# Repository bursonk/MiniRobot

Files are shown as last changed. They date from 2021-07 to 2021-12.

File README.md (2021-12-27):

# MiniRobot Design
Image of Robot
A mini robot built within sumo robot specifications designed to push blocks outside of the ring.  Built to run autonomous or remotely controlled with Bluetooth, as well as a programmable OLED display for debugging.

## Table of contents
* [General info](#general-info)
* [Technologies](#technologies)
* [Project Status](#project-status)
* [Features](#features)
* [acknowledgements](#acknowledgements)

## General info
This project contains the custom chassis and PCB design files I created for a University Design Project in February 2020. 

## Technologies
* Teensy3.6
* KiCad
* SolidWorks

## Project Status
Due to various manufactures of component boards, location of mounting holes may need to be altered.

### To Do List
- [x] Update files to reflect final design
- [ ] Complete Project Documentation

## Features
The sumo robot features a 10cm X 10cm Chassis.

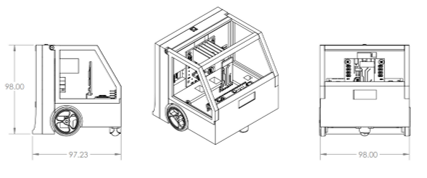
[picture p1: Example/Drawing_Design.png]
Robot Drawing


### Chassis

#### 3D printing

#### Threaded Inserts

### PCB

#### Soldering

#### Wiring and Connections

### Components

### Results

## Acknowledgements
A folder of SolidWorks parts with the electrical components used in the robot is included in this repository. 
Parts in this folder are used for the robot assembly design and were obtained from SolidWorks resources, from the manufacturer, or developed by me.

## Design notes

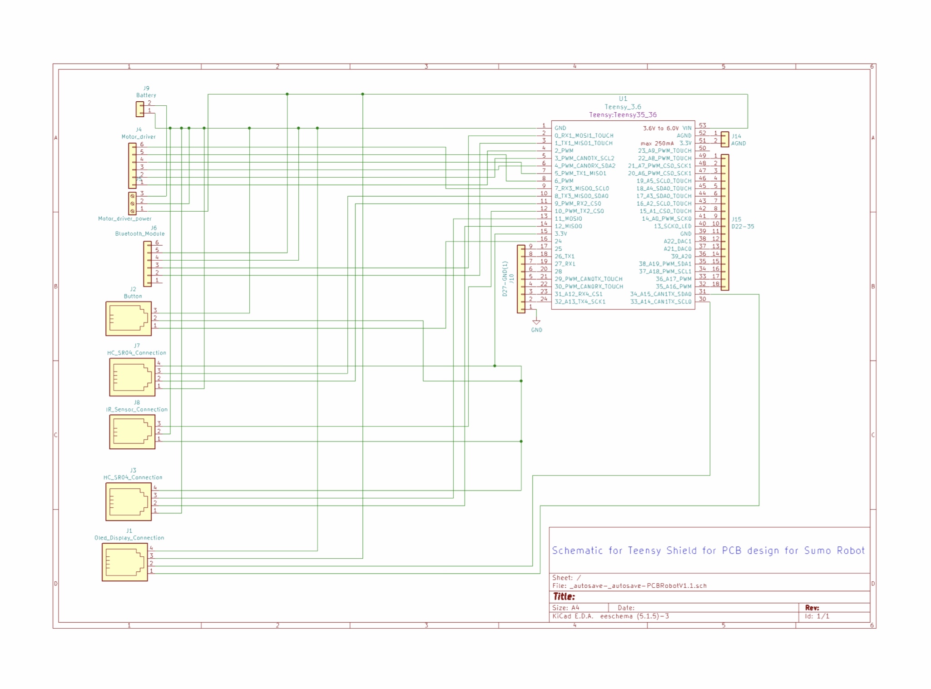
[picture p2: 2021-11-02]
Example/TeensyShieldSchematic.jpg

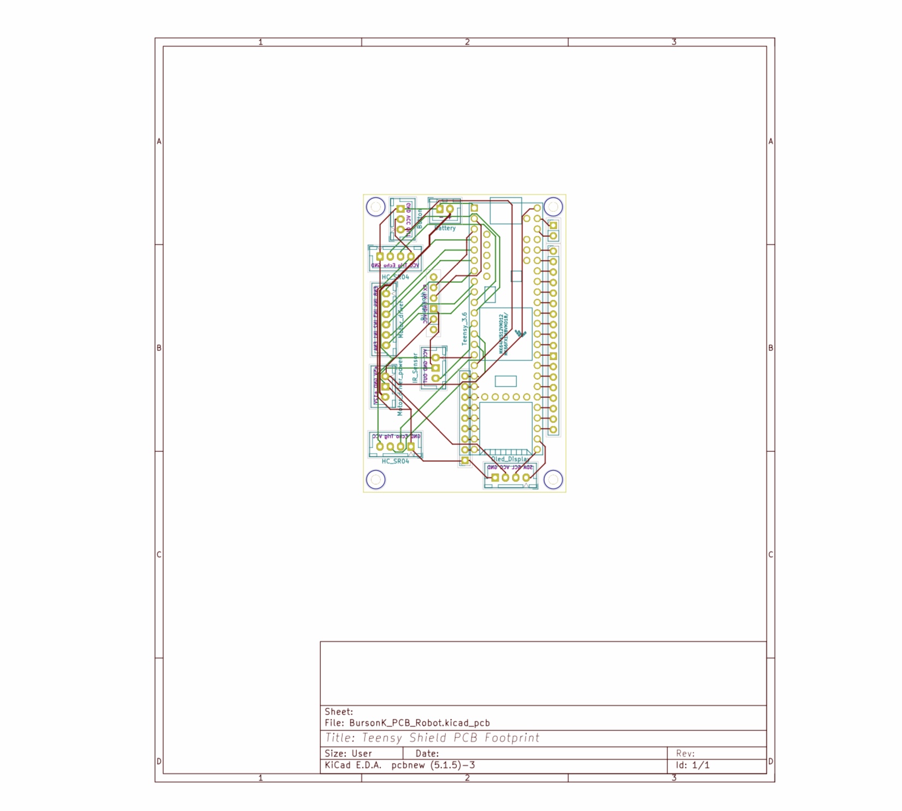
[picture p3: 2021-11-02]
Example/TeensyShieldLayout.jpg

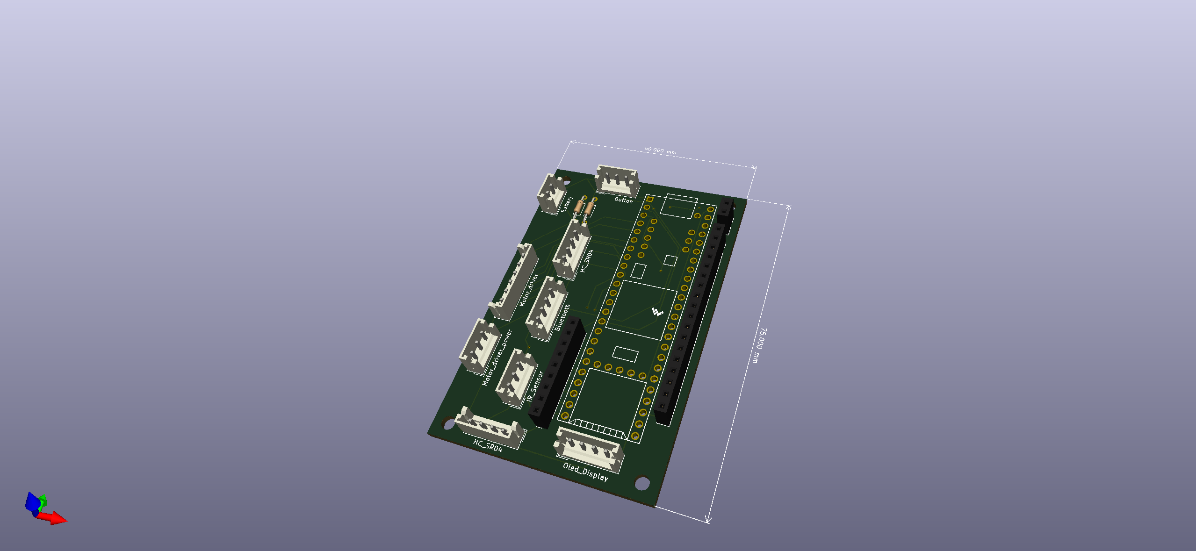
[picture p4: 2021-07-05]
Example/TeensyPCB_1.png

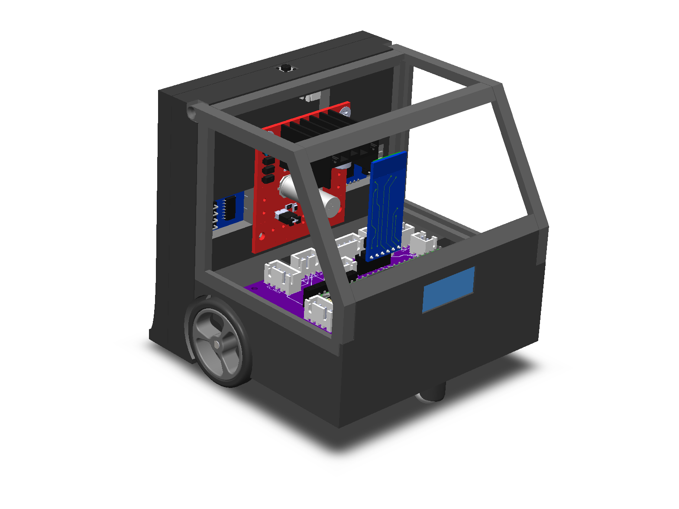
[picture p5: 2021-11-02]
Example/CAD_Robot_1.PNG

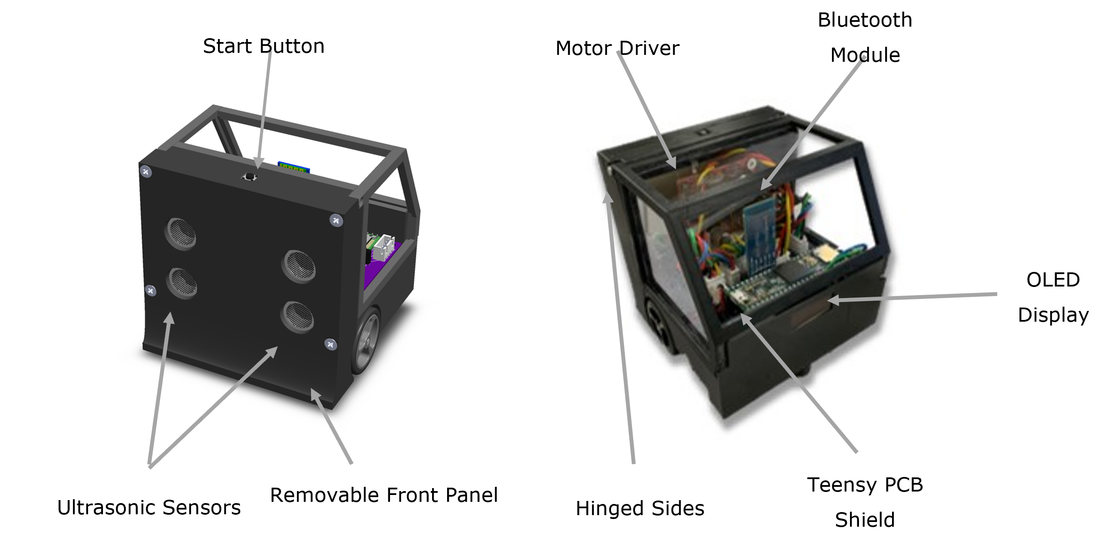
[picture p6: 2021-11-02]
Example/Layout_1.png

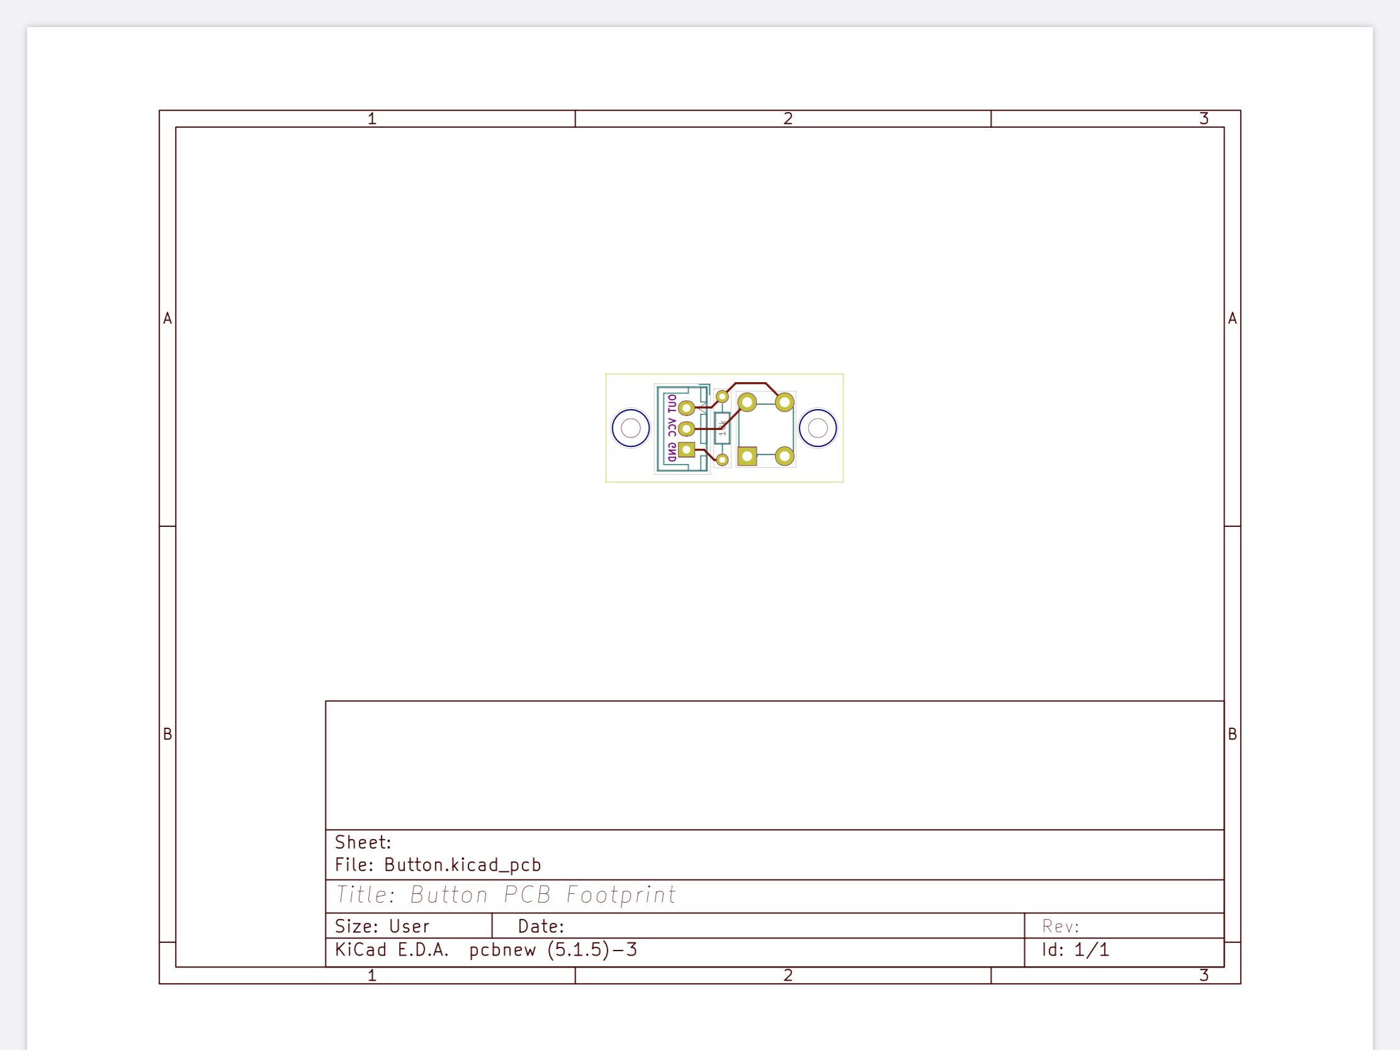
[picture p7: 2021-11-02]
Example/StartButtonLayout.PNG

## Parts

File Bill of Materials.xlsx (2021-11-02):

 | Bill of Materials
Main Category | Sub Category | Purchase Link | Notes | Part Number | Qty | Price | Total Price for Parts | Data Sheet
Microcontroller | Teensy 3.6 | PJRC (https://www.pjrc.com/store/teensy36.html) |  | TEENSY36 | 1 | $29.25 | $29.25 | Here (https://cdn.sparkfun.com/datasheets/Dev/Arduino/Boards/K66P144M180SF5RMV2.pdf)
Electronics | HC-SR04+ Ultrasonic Sensor | Amazon (https://www.amazon.com/gp/product/B07W1GD5F8/ref=ppx_yo_dt_b_asin_title_o05_s00?ie=UTF8&psc=1) | 2pcs included and need 2 | a19052200ux0126 | 1 | $7.73 | $7.73 | Here (https://cdn.sparkfun.com/datasheets/Sensors/Proximity/HCSR04.pdf)
 | IR Infrared Sensor | Amazon (https://www.amazon.com/HiLetgo-Infrared-Avoidance-Reflective-Photoelectric/dp/B07W97H2WS?s=industrial) | 10 pcs included, need 1 | B07W97H2WS | 1 | $7.99 | $7.99 | Here (https://components101.com/sites/default/files/component_datasheet/Datasheet%20of%20IR%20%20Sensor.pdf)
 | HC-05 Bluetooth Module | JSumo (https://www.jsumo.com/hc-05-bluetooth-module-serial-transceiver-module) |  | HC06BT | 1 | $6.85 | $6.85 | Here (http://www.electronicaestudio.com/docs/istd016A.pdf)
 | OLed Display Module | Amazon (https://www.amazon.com/gp/product/B079BN2J8V/ref=ppx_yo_dt_b_asin_title_o01_s00?ie=UTF8&psc=1) | 2pcs included, need 1 | 8541549353 | 1 | $10.99 | $10.99 | Here (https://cdn-shop.adafruit.com/datasheets/SSD1306.pdf)
 | L298N Motor Drive Controller | #VALUE! (https://www.amazon.com/Qunqi-Controller-Module-Stepper-Arduino/dp/B014KMHSW6?hvadid=167139094796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) |  | CECOMINOD012186 | 1 | $6.89 | $6.89 | Here (http://www.handsontec.com/dataspecs/L298N%20Motor%20Driver.pdf)
 | Mini Gear Motor | Pololu (https://www.pololu.com/product/997) | 150:1 Gearmotor - 6V | 997 | 2 | $15.95 | $31.90 | Here (https://www.pololu.com/file/0J1487/pololu-micro-metal-gearmotors-rev-4-2.pdf)
 | Tactile SPST Switch | ResiStore (https://resi.store/inventory/item.php?plu=855) |  | 855 | 1 | $0.05 | $0.05 | Here (https://resi.store/datasheets/spst.pdf)
 | 10k Resistor | ResiStore (https://resi.store/inventory/item.php?plu=190) |  | 190 | 1 | $0.05 | $0.05 | Here (https://resi.store/datasheets/resistor.pdf)
 | 9V Battery Holder with Switch | LedSupply (https://www.ledsupply.com/accessories/9v-battery-holder-switch-leads) |  | BH-9V-SWITCH | 1 | $1.69 | $1.69 | Here (https://www.ledsupply.com/accessories/9v-battery-holder-switch-leads)
Assembly | Wheel 32X7mm - Pair | Pololu (https://www.pololu.com/product/1087) |  | 1087 | 1 | $2.95 | $2.95 | Here (https://www.pololu.com/product-info-merged/1087)
 | Caster Ball | Pololu (https://www.pololu.com/product/950) | Pololu Ball Caster with 3/8″ Plastic Ball | 950 | 1 | $1.99 | $1.99 | Here (https://www.pololu.com/file/0J1636/pololu-ball-caster-with-0-375in-ball.pdf)
 | B6B-XH-A(LF)(SN) | Digikey (https://www.digikey.com/product-detail/en/jst-sales-america-inc/B6B-XH-A-LF-SN/455-2271-ND/1000381) | JST XH Connector 6x1 - Male | 455-2271-ND | 2 | $0.27 | $0.54 | Here (http://www.jst-mfg.com/product/pdf/eng/eXH.pdf)
 | B5B-XH-A(LF)(SN) | Digikey (https://www.digikey.com/product-detail/en/jst-sales-america-inc/B5B-XH-A-LF-SN/455-2270-ND/1530483) | JST XH Connector 5x1 - Male | 455-2270-ND | 1 | $0.25 | $0.25 | Here
 | B4B-XH-A(LF)(SN) | Digikey (https://www.digikey.com/product-detail/en/jst-sales-america-inc/B4B-XH-A-LF-SN/455-2249-ND/1651047) | JST XH Connector 4x1 - Male | 455-2249-ND | 6 | $0.21 | $1.26 | Here
 | B3B-XH-A(LF)(SN) | Digikey (https://www.digikey.com/product-detail/en/jst-sales-america-inc/B3B-XH-A-LF-SN/455-2248-ND/1651046) | JST XH Connector 3x1 - Male | 455-2248-ND | 5 | $0.19 | $0.95 | Here
 | B2B-XH-A(LF)(SN) | Digikey (https://www.digikey.com/product-detail/en/jst-sales-america-inc/B2B-XH-A-LF-SN/455-2247-ND/1651045) | JST XH Connector 2x1 - Male | 455-2247-ND | 1 | $0.15 | $0.15 | Here
 | XHP - 6 | Digikey (https://www.digikey.com/product-detail/en/jst-sales-america-inc/XHP-6/455-2218-ND/1651016) | JST XH Female Connector Housing 6x1 | 455-2218-ND | 2 | $0.14 | $0.28 | Here
 | XHP - 5 | Digikey (https://www.digikey.com/product-detail/en/jst-sales-america-inc/XHP-5/455-2268-ND/1125486) | JST XH Female Connector Housing 5x1 | 455-2268-ND | 1 | $0.12 | $0.12 | Here
 | XHP - 4 | Digikey (https://www.digikey.com/product-detail/en/jst-sales-america-inc/XHP-4/455-2267-ND/683353) | JST XH Female Connector Housing 4x1 | 455-2267-ND | 6 | $0.10 | $0.60 | Here
 | XHP - 3 | Digikey (https://www.digikey.com/product-detail/en/jst-sales-america-inc/XHP-3/455-2219-ND/1651017) | JST XH Female Connector Housing 3x1 | 455-2219-ND | 5 | $0.10 | $0.50 | Here
 | XHP - 2 | Digikey (https://www.digikey.com/product-detail/en/jst-sales-america-inc/XHP-2/455-2266-ND/555485) | JST XH Female Connector Housing 2x1 | 455-2266-ND | 1 | $0.10 | $0.10 | Here
 | Brass Knurled Threaded Insert | Amazon (https://www.amazon.com/gp/product/B0784VYCYY/ref=ppx_yo_dt_b_asin_title_o04_s00?ie=UTF8&psc=1) | 250-Pcs M2 / M3 /M4 Assortment Kit | HBN-250 | 1 | $15.98 | $15.98 | Here (https://www.pemnet.com/bulletins_A4/sidata_A4.pdf)
 | M1.6 Thread Brass Knurled Insert | Amazon (https://www.amazon.com/gp/product/B07TTQXVQH/ref=ppx_yo_dt_b_asin_title_o06_s00?ie=UTF8&psc=1) | 50PCS M1.6 x 4mm | QXAD0072 | 1 | $4.59 | $4.59 | Here
 | M1.6 x 6mm Screws | Wilco | M1.6 screw 6mm length |  | 8 | $0.20 | $1.60
 | M2 x 4mm Screws | HomeDepot (https://www.homedepot.com/p/Everbilt-M2-0-4-x-4-mm-Phillips-Flat-Head-Stainless-Steel-Machine-Screw-2-Pack-843438/204852270) | 4mm Phillips flathead machine screw 2pcs | 794439 | 3 | $0.40 | $1.20
 | M2 x 8mm Screws | HomeDepot (https://www.homedepot.com/p/Everbilt-M2-0-4-x-8-mm-Phillips-Flat-Head-Stainless-Steel-Machine-Screw-2-Pack-843458/204852267) | 8mm Phillips flathead machine screw 2pcs | 795552 | 1 | $0.54 | $0.54
 | M2 x 10mm Screws | HomeDepot (https://www.homedepot.com/p/Everbilt-M2-0-4-x-10-mm-Phillips-Flat-Head-Stainless-Steel-Machine-Screw-2-Pack-843468/204852266) | 10mm Phillips flathead machine screw 2pcs | 790787 | 1 | $0.40 | $0.40
 | M3 x 6mm Screws | HomeDepot (https://www.homedepot.com/p/Everbilt-M3-0-5-x-6-mm-Phillips-Flat-Head-Zinc-Plated-Machine-Screw-3-Pack-841638/204849605) | 6mm Phillips flathead machine screw 3pcs | 903113 | 3 | $0.50 | $1.50
 | M3 x 8mm Screws | HomeDepot (https://www.homedepot.com/p/Everbilt-M3-0-5-x-8-mm-Phillips-Flat-Head-Stainless-Steel-Machine-Screw-2-Pack-843618/204849557) | 8mm Phillips flathead machine screw 2pcs | 513007 | 1 | $0.54 | $0.54
 | M3 x 10mm Screws | HomeDepot (https://www.homedepot.com/p/Everbilt-M3-0-5-x-10-mm-Phillips-Flat-Head-Stainless-Steel-Machine-Screw-2-Pack-843628/204849556) | 10mm Phillips flathead machine screw 2pcs | 796645 | 3 | $0.65 | $1.95
Custom Items | 3D Printed Frame
 | Teensy Shield - PCB Board
 | Button Module - PCB Board
 | Acrylic Cut Windows
 | Total Cost For Materials |  |  |  | $141.38

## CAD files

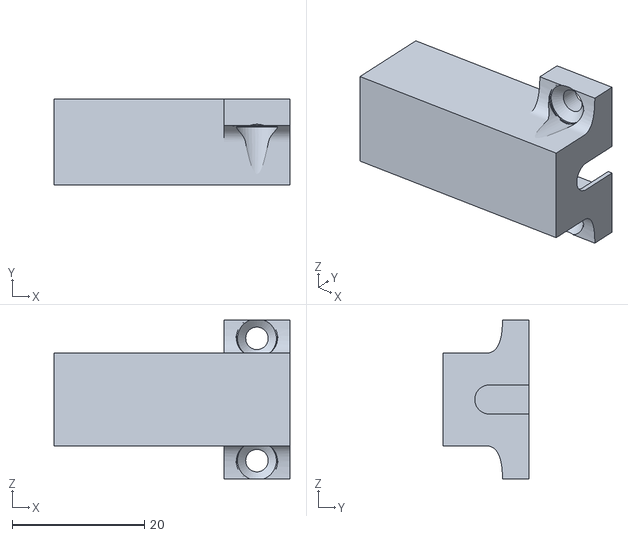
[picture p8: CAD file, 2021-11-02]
Custom Chassis Parts (.stl)/mount_v2.STL
35.7 x 13.0 x 24.0

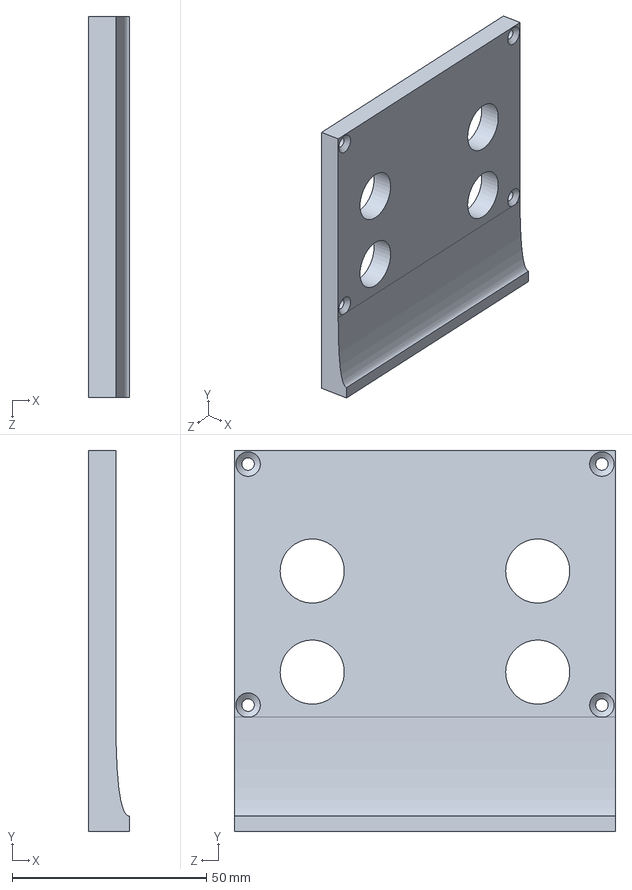
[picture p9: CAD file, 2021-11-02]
Robot SolidWorks Files/Front_Shield.SLDPRT
10.5 x 98.0 x 98.0 mm

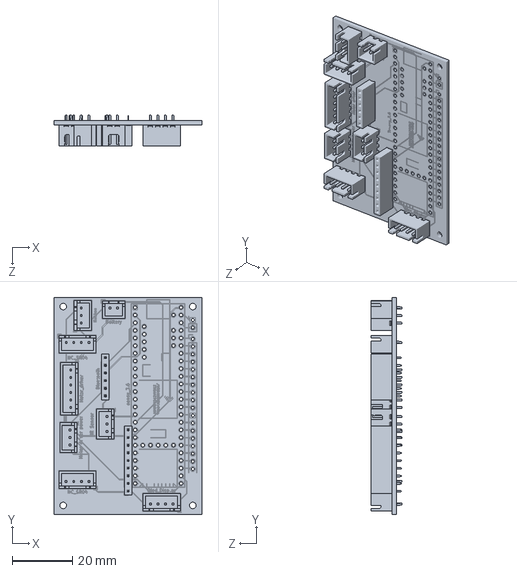
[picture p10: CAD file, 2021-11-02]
Robot SolidWorks Files/Purchased Components Parts/PCB_Bot.SLDPRT
49.0 x 72.0 x 10.4 mm

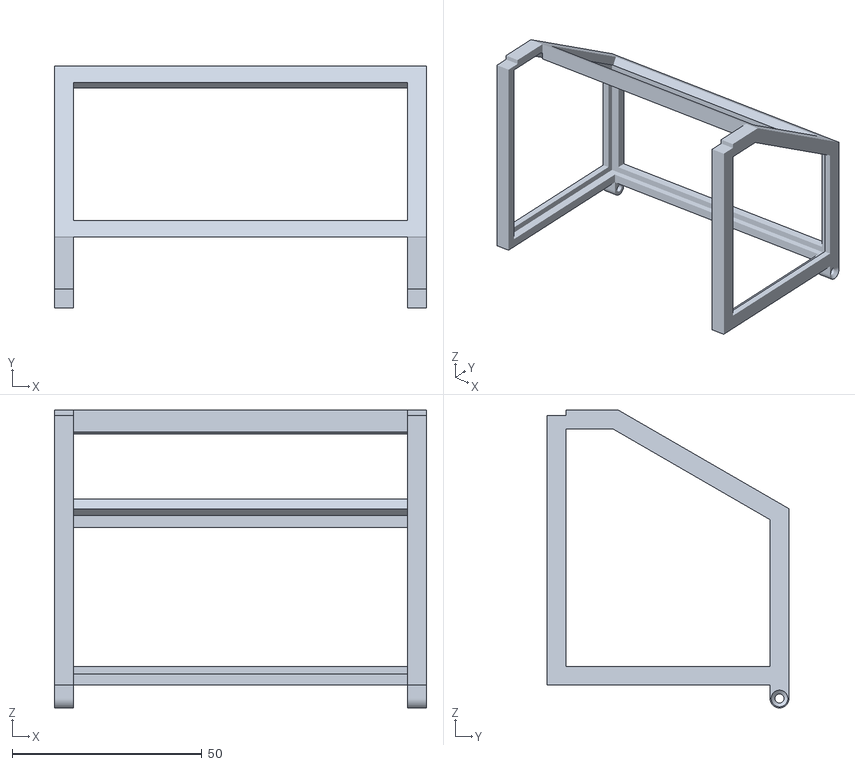
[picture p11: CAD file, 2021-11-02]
Custom Chassis Parts (.stl)/TopV2.STL
98.0 x 63.7 x 78.5

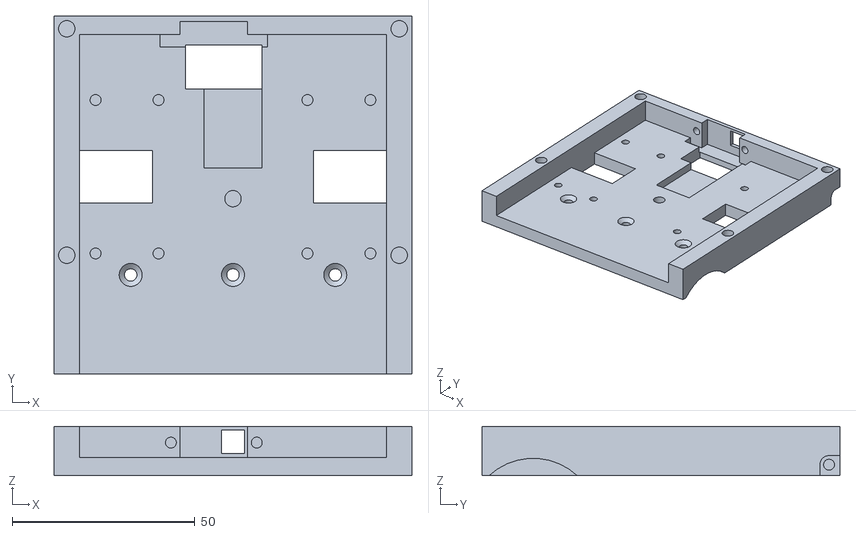
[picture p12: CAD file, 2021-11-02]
Custom Chassis Parts (.stl)/SensorMount_V2.STL
98.0 x 98.0 x 13.5

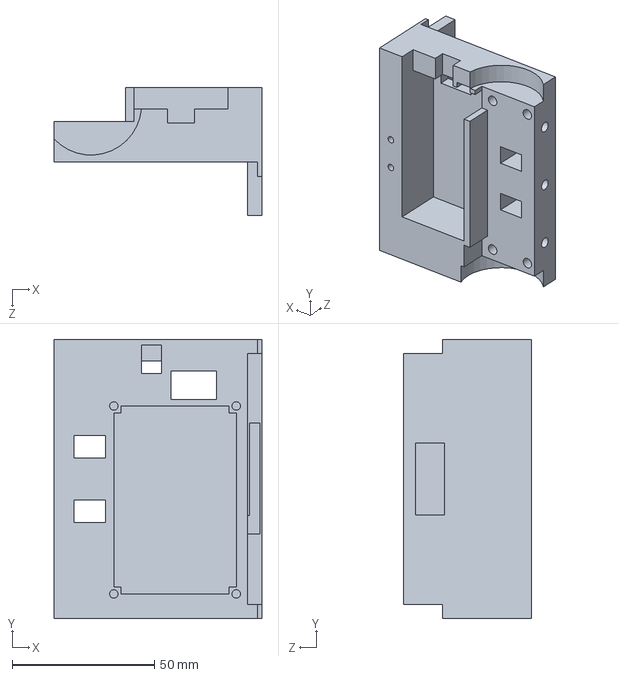
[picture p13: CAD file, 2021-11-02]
Robot SolidWorks Files/Base.SLDPRT
73.0 x 98.0 x 45.0 mm

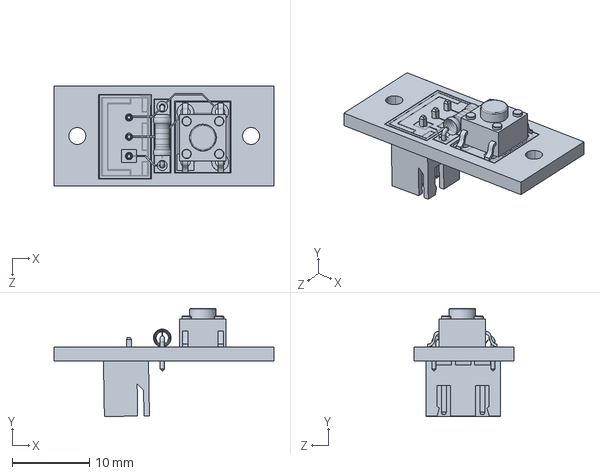
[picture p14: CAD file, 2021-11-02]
Robot SolidWorks Files/Purchased Components Parts/Button_PCB.SLDPRT
28.5 x 14.0 x 13.0 mm

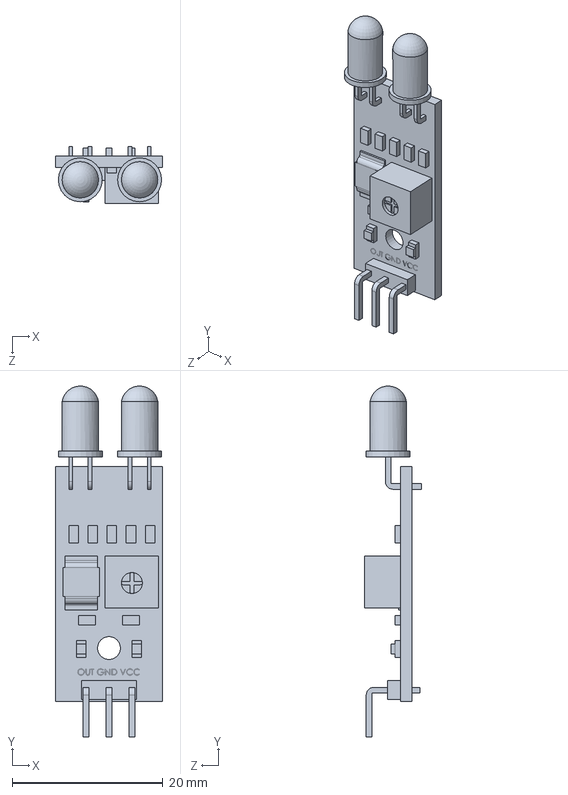
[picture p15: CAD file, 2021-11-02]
Robot SolidWorks Files/Purchased Components Parts/IR Sensor (FC51).SLDPRT
14.2 x 46.6 x 7.62 mm

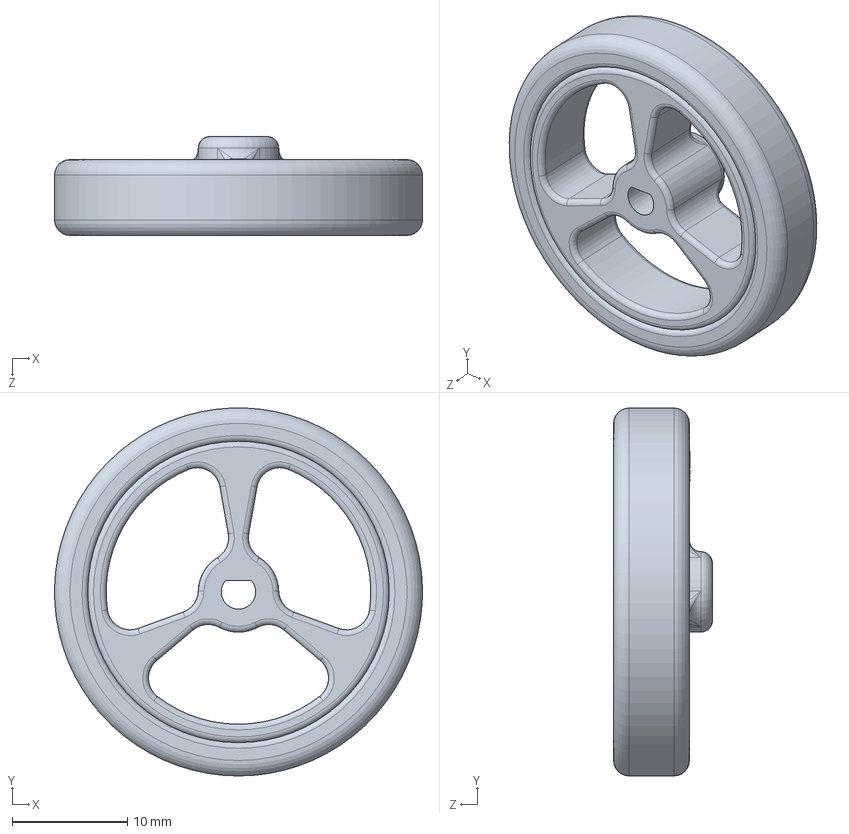
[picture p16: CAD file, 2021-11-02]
Robot SolidWorks Files/Purchased Components Parts/pololu-wheel-32x7mm-black.SLDPRT
32.0 x 32.0 x 8.60 mm

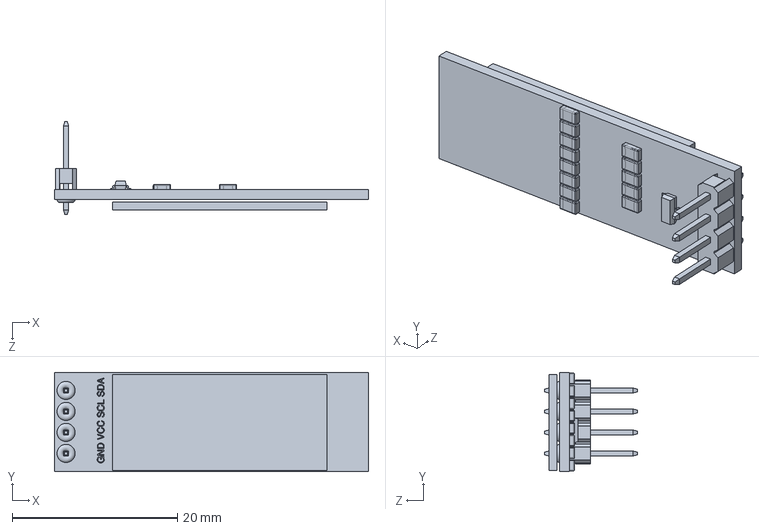
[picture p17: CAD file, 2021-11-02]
Robot SolidWorks Files/Purchased Components Parts/OLED 128x32 Display.SLDPRT
38.0 x 12.0 x 11.2 mm

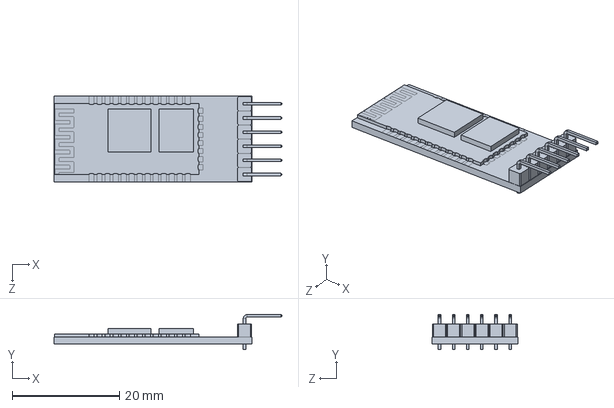
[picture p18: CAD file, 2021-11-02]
Robot SolidWorks Files/Purchased Components Parts/HC-05_Bluetooth.SLDPRT
42.6 x 6.55 x 16.0 mm

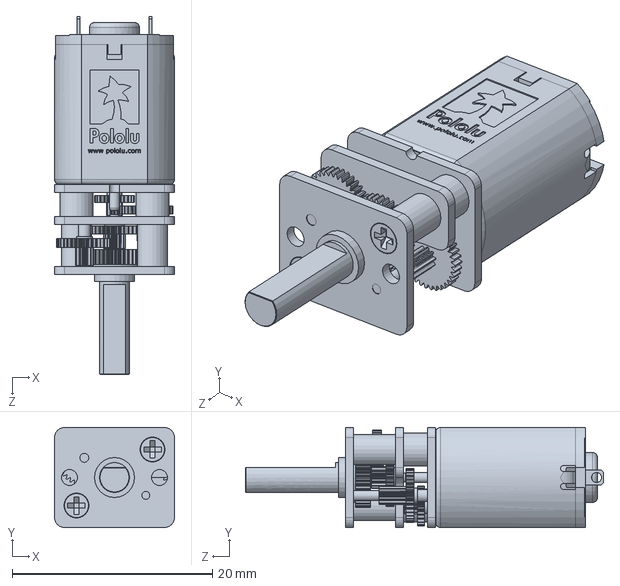
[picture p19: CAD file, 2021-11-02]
Robot SolidWorks Files/Purchased Components Parts/micro-metal-gearmotor-standard (1).SLDPRT
12.0 x 10.0 x 35.8 mm

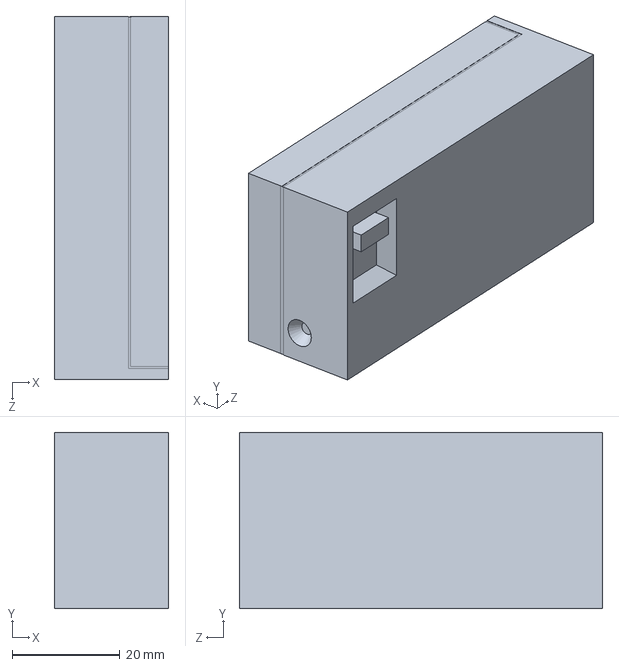
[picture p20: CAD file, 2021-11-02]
Robot SolidWorks Files/Purchased Components Parts/BatteryEnclosure.SLDPRT
21.2 x 32.8 x 67.5 mm

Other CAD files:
Robot SolidWorks Files/mount_v2.SLDPRT
Custom Chassis Parts (.stl)/Front_ShieldV2.STL
Robot SolidWorks Files/TopV2.SLDPRT
Custom Chassis Parts (.stl)/Base_V2.STL
Robot SolidWorks Files/SensorMount.SLDPRT
Custom Chassis Parts (.stl)/Archive/Base.STL
Custom Chassis Parts (.stl)/Archive/Front_Shield.STL
Custom Chassis Parts (.stl)/Archive/SensorMount.STL
Custom Chassis Parts (.stl)/Archive/SensorMountV2.1.STL
Custom Chassis Parts (.stl)/Archive/Side1.STL
Custom Chassis Parts (.stl)/Archive/Side2.STL
Custom Chassis Parts (.stl)/Archive/Sides.STL
Custom Chassis Parts (.stl)/Archive/Top1.STL
Custom Chassis Parts (.stl)/Archive/Top2.STL
Custom Chassis Parts (.stl)/Archive/Top3.STL
Custom Chassis Parts (.stl)/Archive/TopV2.1.STL
Custom Chassis Parts (.stl)/Archive/mount.STL
Robot SolidWorks Files/Archived Chassis SolidWorks Parts/Side1.SLDPRT
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

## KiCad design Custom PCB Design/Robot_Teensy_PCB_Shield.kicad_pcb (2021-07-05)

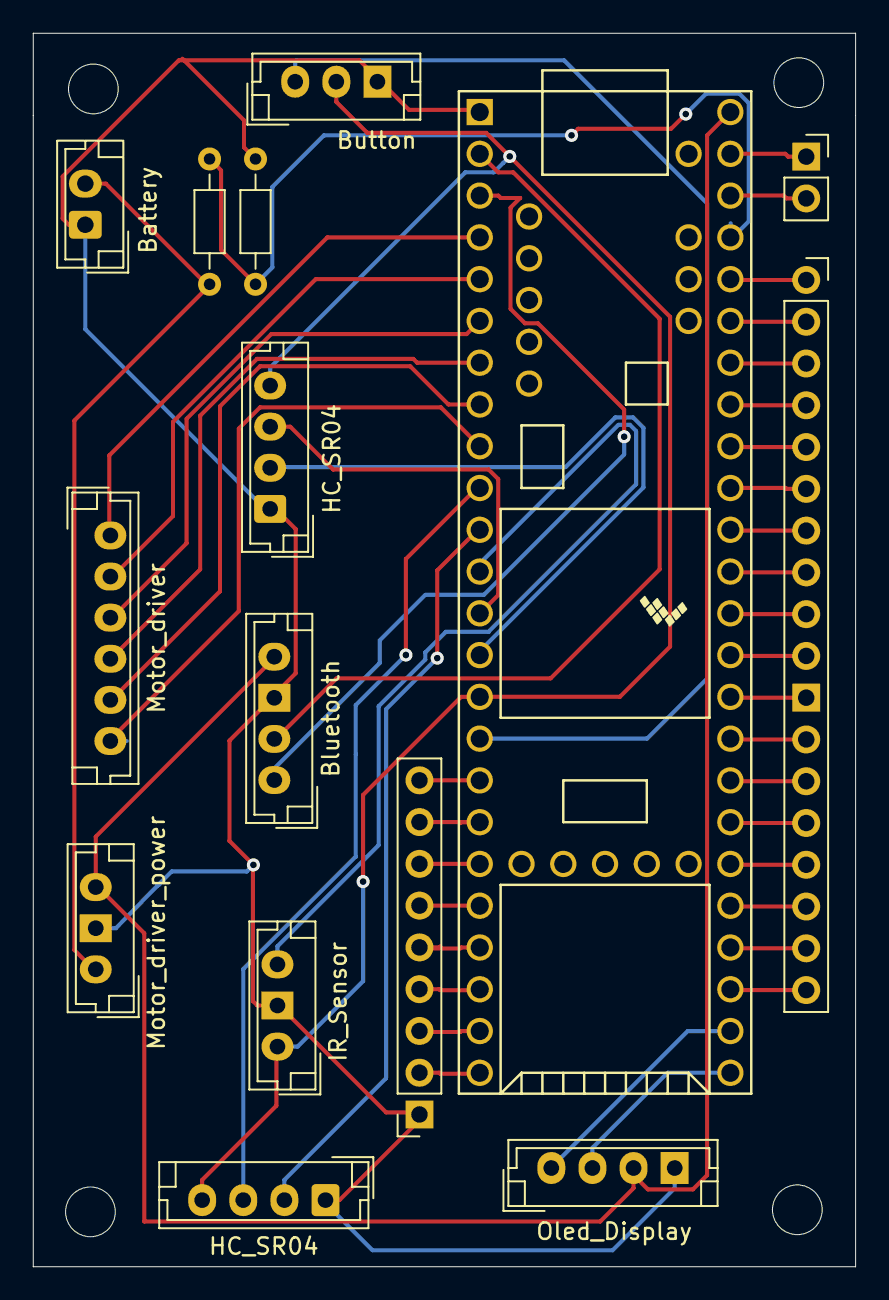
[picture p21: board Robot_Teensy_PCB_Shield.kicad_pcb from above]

Board: 2 copper layers, 50.0 x 75.0 mm, 9 parts (0 on the bottom side), 4 nets.

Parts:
Battery: JST_EH_B2B-EH-A_1x02_P2.50mm_Vertical
Bluetooth: JST_EH_B4B-EH-A_1x04_P2.50mm_Vertical
Button: JST_EH_B3B-EH-A_1x03_P2.50mm_Vertical
HC_SR04, HC_SR04#2: JST_EH_B4B-EH-A_1x04_P2.50mm_Vertical
IR_Sensor: JST_EH_B3B-EH-A_1x03_P2.50mm_Vertical
Motor_driver: JST_EH_B6B-EH-A_1x06_P2.50mm_Vertical
Motor_driver_power: JST_EH_B3B-EH-A_1x03_P2.50mm_Vertical
Oled_Display: JST_EH_B4B-EH-A_1x04_P2.50mm_Vertical

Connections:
unnamed: Bluetooth.VCC, Motor_driver_power.+5V, Oled_Display.VCC
unnamed: Battery.-, Bluetooth.GND, Button.GND, HC_SR04.GND, HC_SR04#2.GND, IR_Sensor.GND, Motor_driver_power.GND, Oled_Display.GND
unnamed: Button.VCC, HC_SR04.VCC, HC_SR04#2.VCC, IR_Sensor.VCC
unnamed: Battery.+, Motor_driver_power.+12V

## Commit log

2021-07-05 Robot SolidWorks Files
    Custom Built from Scratch module robot design. Initial File Upload.
    [Base.SLDPRT, Base.STL, BatteryEnclosure.SLDPRT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]
2021-07-05 PCB Design
    Adding custom PCB teensy shield design for components
    [PCBRobot.kicad_pcb, PCBRobot.sch, V1.1.kicad_pcb]
2021-11-02 Add files via upload
    Updating to reflect Chassis Design
    [Base_V2.STL, Front_ShieldV2.STL, SensorMount_V2.STL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]
2021-11-02 Robot SolidWorks Files
    Updating files to reflect final project results
    [Base.SLDPRT, Base.STL, Base_V2.STL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]
2021-11-02 Robot Design Files
    Updating to reflect final Robot design
    [Bill of Materials.xlsx, ButtonBoard.kicad_pcb, PCBRobot.kicad_pcb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]
2021-11-02 Robot Design Files
    [Robot_Start_Button_PCB.kicad_pcb, Robot_Teensy_PCB_Shield.kicad_pcb, Robot_Teensy_PCB_Shield.sch]
